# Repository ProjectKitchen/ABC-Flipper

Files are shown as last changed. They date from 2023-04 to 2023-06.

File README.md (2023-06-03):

# ABC-Flipper

**A Pinball Machine for solving Anagram Puzzles! (In cooperation with David Moises)**

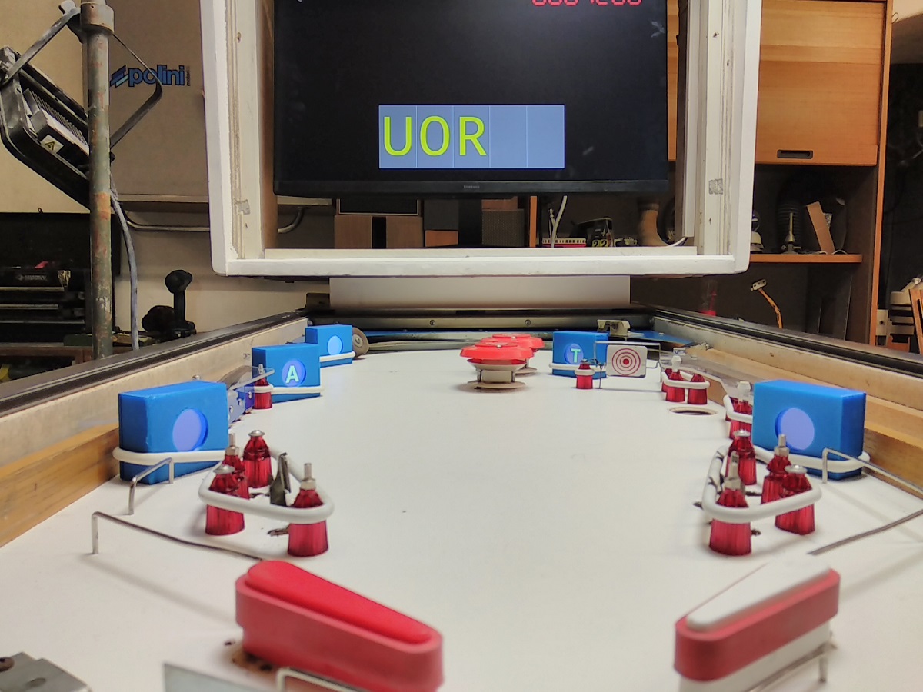
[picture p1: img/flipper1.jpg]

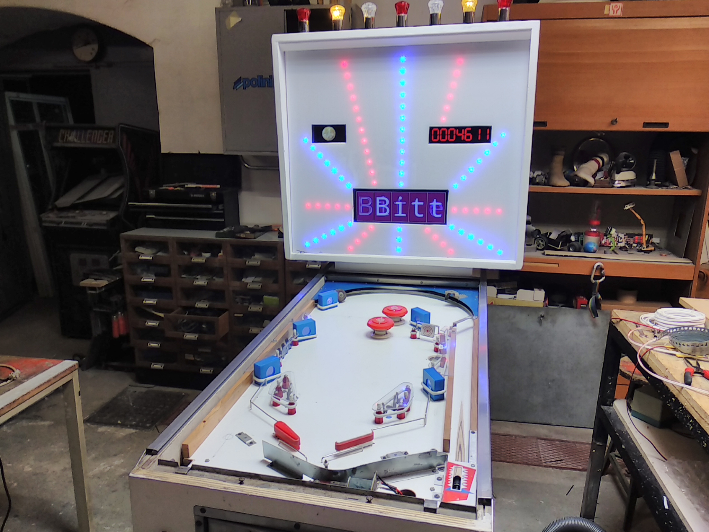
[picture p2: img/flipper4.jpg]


# Preparation

## Material

| Nr.  | Description | 
| ---- | --- |
| 1 | 1 x RaspberryPi 4 | 
| 2 | 1 x Teensy2.0++ (or Teensy3.2) |
| 3 | 5 x TeensyLC for Minidisplay Screens | 
| 4 | 2 x 8-Relay Module for Arduino | 
| 5 | 5 x SPI LCD Display (ST7735, 160x128, SPI) | 
| 6 | Breadboard, jumper wires, buttons/reed switches | 

## Install SW-Requirements

| Nr.  | Description | Source |
| ---- | --- | --- |
| 1 | Python3 | Open an command shell window and check your python/python3 version: `python3 --version'. The recommended version is python3.8 or newer |
| 2 | pyserial library | Install via pip: `pip3 install pyserial` |
| 3 | pygame library | Install via pip: `pip3 install pygame` |
| 4 | pillow library | Install via pip: `pip3 install pillow` |
| 5 | Arduino IDE | Download from Arduino website https://www.arduino.cc |
| 6 | Teensyduino Add-On | Download from website https://www.pjrc.com/teensy/td_download.html |
| 7 | Adafruit_GFX library | Install using Arduino library manager |
| 8 | Adafruit_ST7735 library | Install using Arduino library manager |

## Deploy Software

* Build and flash the Arduino code (folders src/arduinoIO and src/teensyLC_LCD) 
* Install custum fonts (copy segment.ttf to folder ~/.fonts, update font cache)
* run python3 flipper.py
* install startup script: sudo nano /etc/xdg/autostart/display.desktop, add:
    [Desktop Entry]
    Name=ABCFlipper
    Exec=/usr/bin/python3 /home/pi/ABC-Flipper/src/flipper.py

* configure read-only filesystem (Preferences -> RaspberryPi Configuration -> Performance)

## More photos

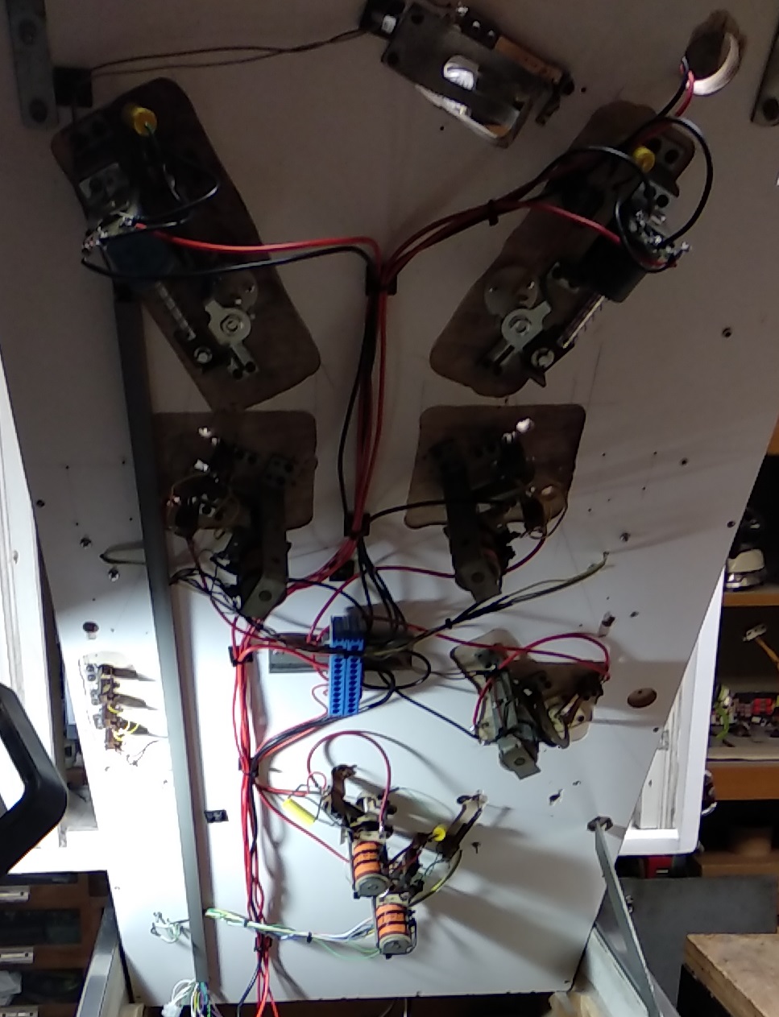
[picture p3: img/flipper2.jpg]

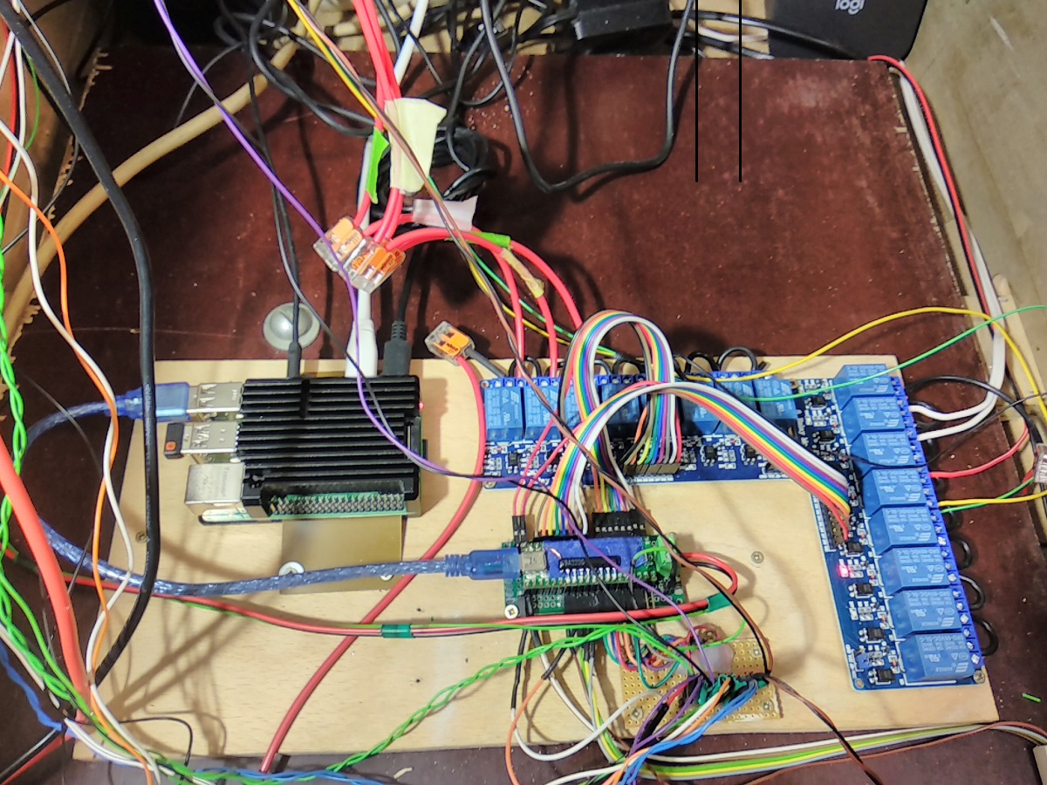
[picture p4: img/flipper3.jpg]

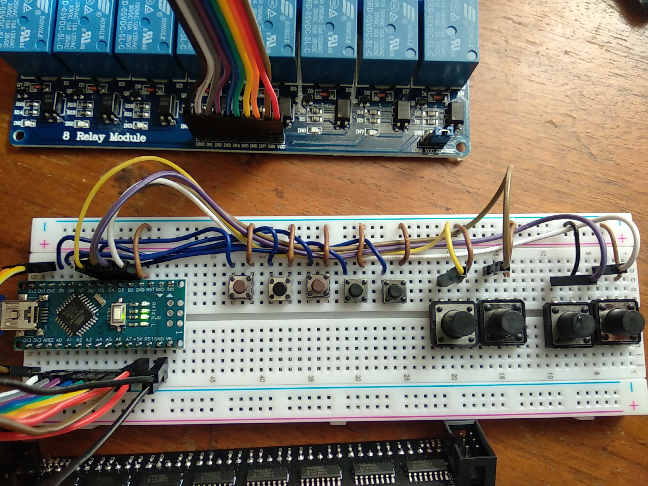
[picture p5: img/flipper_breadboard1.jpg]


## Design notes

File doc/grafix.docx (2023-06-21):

Anleitung:

Ziel des Spieles ist es, 5 Buchstaben zu treffen und daraus Worte zu bilden.
Das Spiel beginnt durch den Einwurf eines Zoomi-Coins. Pro Zoomi-Coin werden 3 Kugeln freigeschalten. Es gibt zwei unterschiedliche Spielvarianten: “Normal” und “Superhirn”. Den Superhin-Modus erkennt man daran, dass vor Spielbeginn abwechselnd der Zoomi-Coin und das Gehirn-Symbol am Flipper-Display abgebildet werden. Der Modus kann durch den Schalter im Inneren des Flippers gewechselt werden.

Spielmodus “Normal”: Getroffene Buchstaben erscheinen sofort an der richtigen Stelle des Wortes. Wird das Wort erraten, so erhält das erfolgreiche Team 1-5 Punkte (je mehr Buchstaben bereits gelöst waren, desto weniger Punkte!)

Spielmodus “Superhirn”: Buchstaben erscheinen in der Reihenfolge, in der sie getroffen wurden. Sobald alle 5 Buchstaben gesammelt wurden, ändert sich die Funktion der linken und rechten Flipper Taste: diese Tasten verschieben nun die Position eines Buchstaben! Eine Betätigung der FIX-Taste (an der Vorderseite) wechselt zum nächsten Buchstaben. Kann ein sinnvolles Anagramm gebildet werden, so erhält das erfolgreiche Team 5 Punkte, und die Kugel kommt zurück ins Spiel - verstreicht jedoch die verfügbare Zeit, ohne dass ein Wort gebildet werden konnte, geht die Kugel verloren!

Wird das Joker-Feld getroffen, werden alle 5 Buchstaben sogleich angezeigt. (Im Normalmodus wird dadurch das Wort gelöst, und das Team erhält 5 Punkte)

Wird ein Punkterekord (Highscore) am Flipper erzielt, kann der Name (bzw. die Initialen) eingegeben werden. Der aktuelle Buchstabe wird dabei durch Betätigen der linken oder rechten Flipper-Taste geändert, eine Betätigung der FIX-Taste wechselt zum nächsten Buchstaben.
Der Flipper kann auch in Teams gespielt werden: dabei versuchen alle Team-Mitglieder, das richtige Wort zu erraten!
Nach jedem Spiel kommt eine Person aus dem nächsten Team an die Reihe, die Punkte pro Team werden ggf. auf einem Zettel addiert.
(Diese manuelle Punktezählung ist unabhängig von der Punktezahl, die am Flipper erreicht wird.)

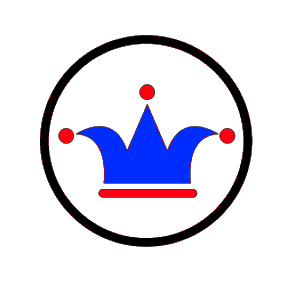
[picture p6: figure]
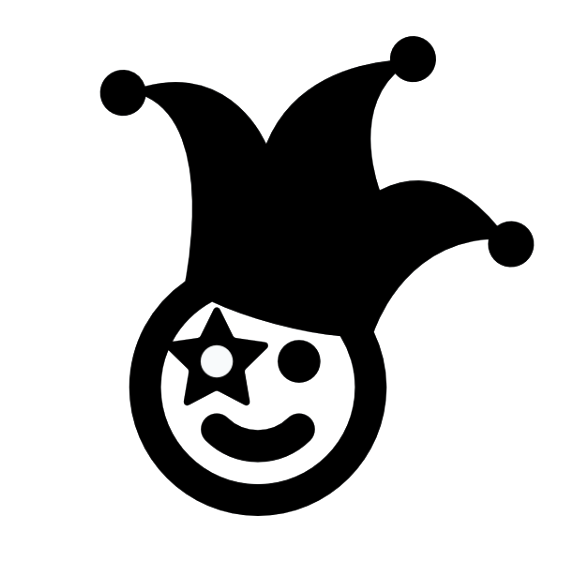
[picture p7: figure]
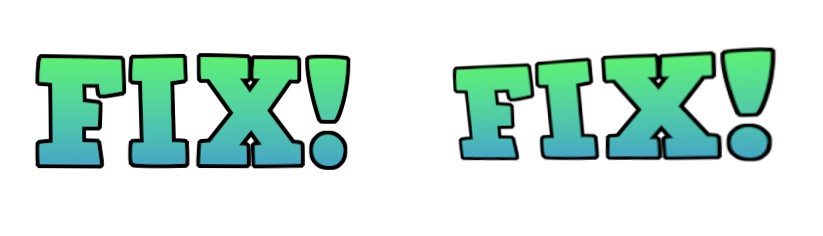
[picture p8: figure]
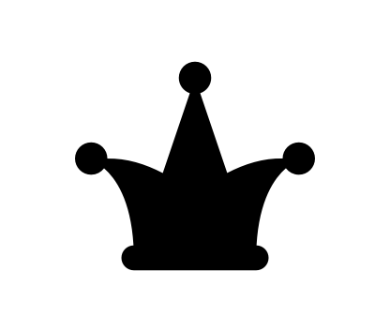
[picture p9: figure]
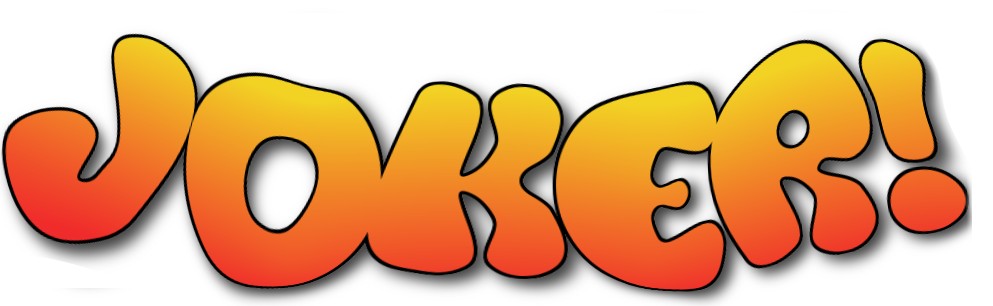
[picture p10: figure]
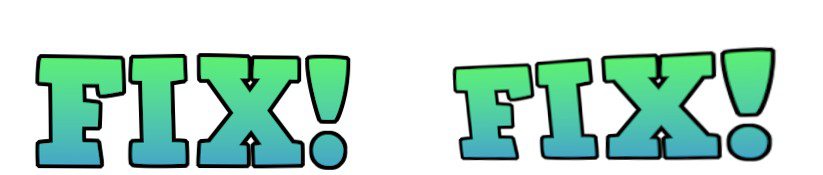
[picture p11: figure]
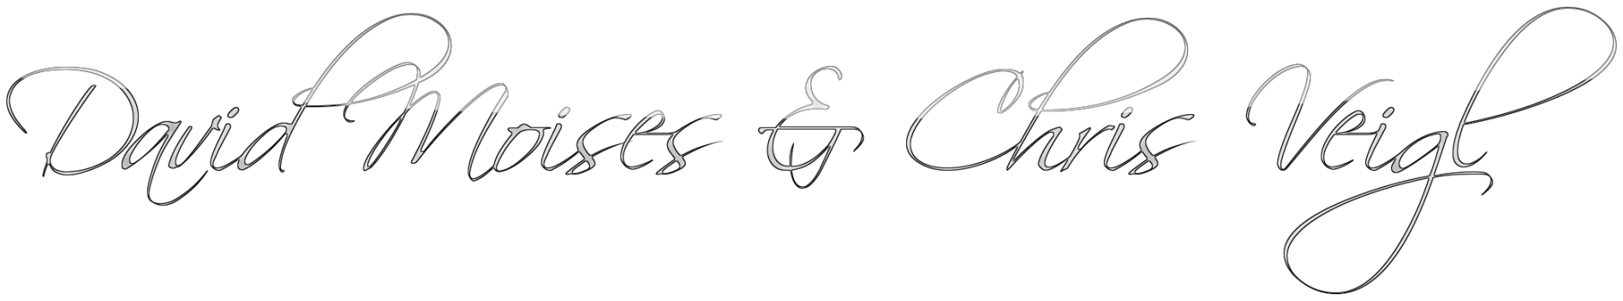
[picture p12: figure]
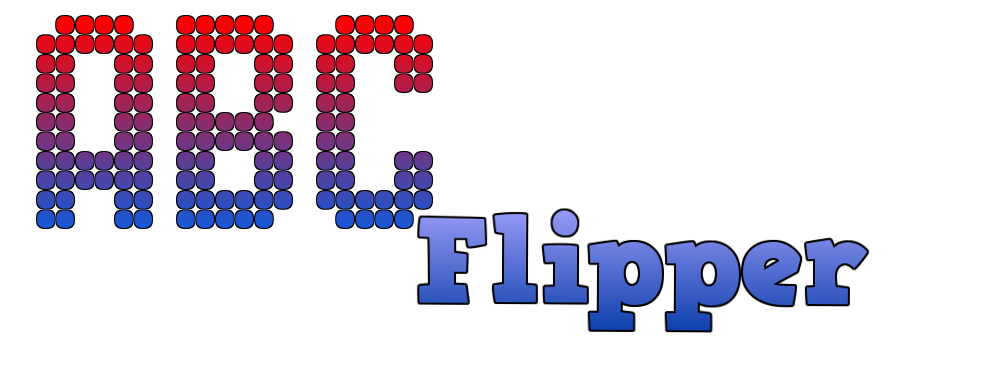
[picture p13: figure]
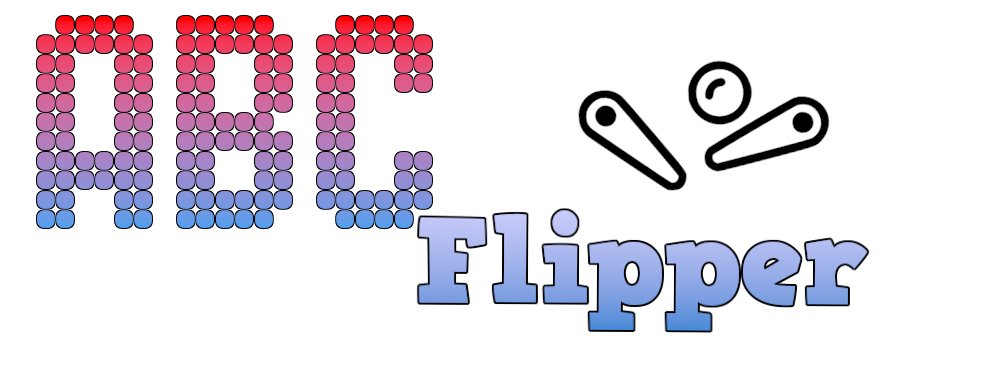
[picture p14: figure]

1. Wirf einen Zoomi ein (für 3 Kugeln)
2. Triff die Buchstaben!
3. Errate das Wort!
4. Bei Rekord: gib deinen Namen ein!

1. Wirf einen Zoomi ein!
2. Triff die Buchstaben!
3. Errate das Wort!
4. Bei Rekord: gib deinen Namen ein!

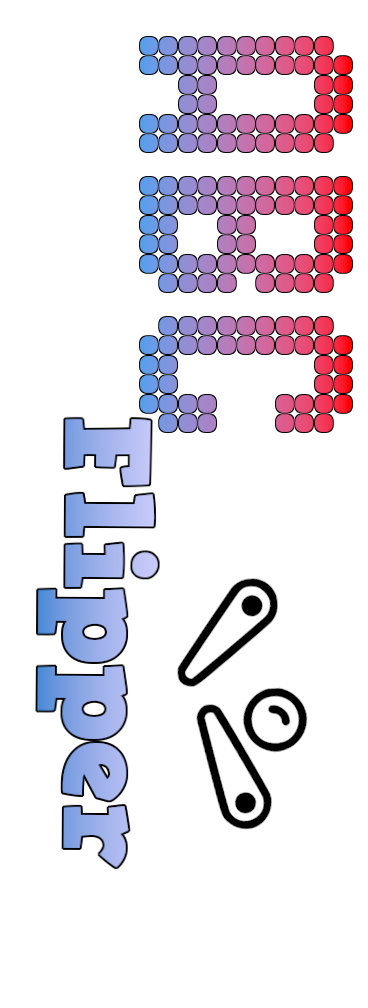
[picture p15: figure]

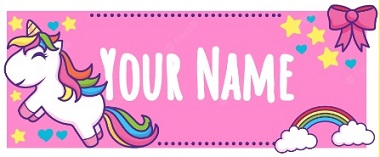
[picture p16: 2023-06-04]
img/name.jpg

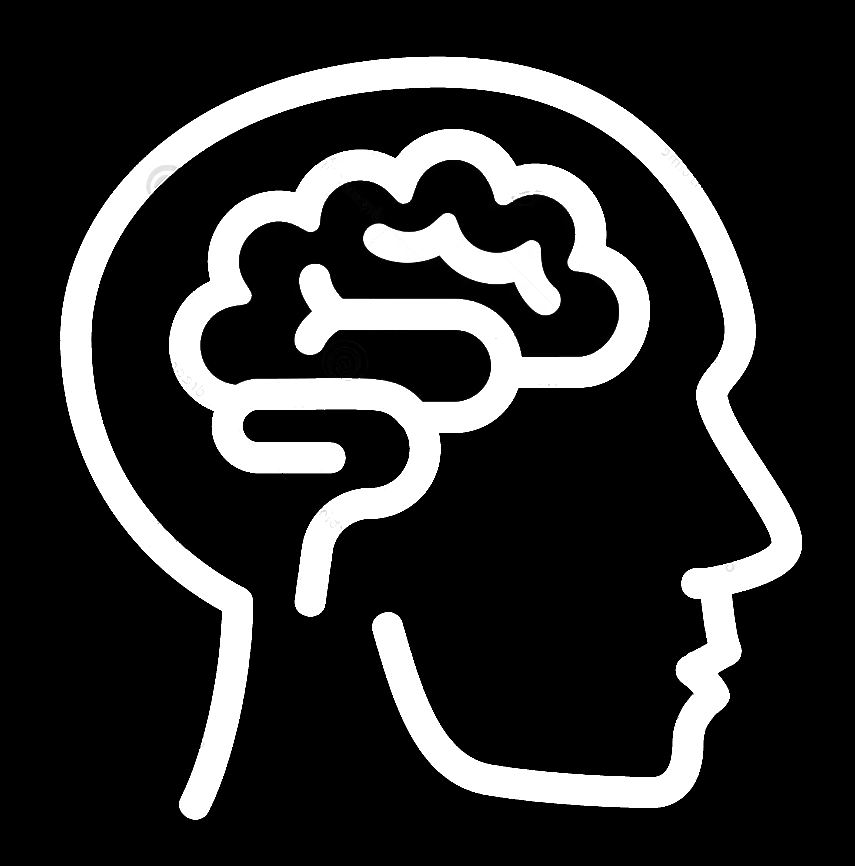
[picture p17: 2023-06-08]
img/brain.png

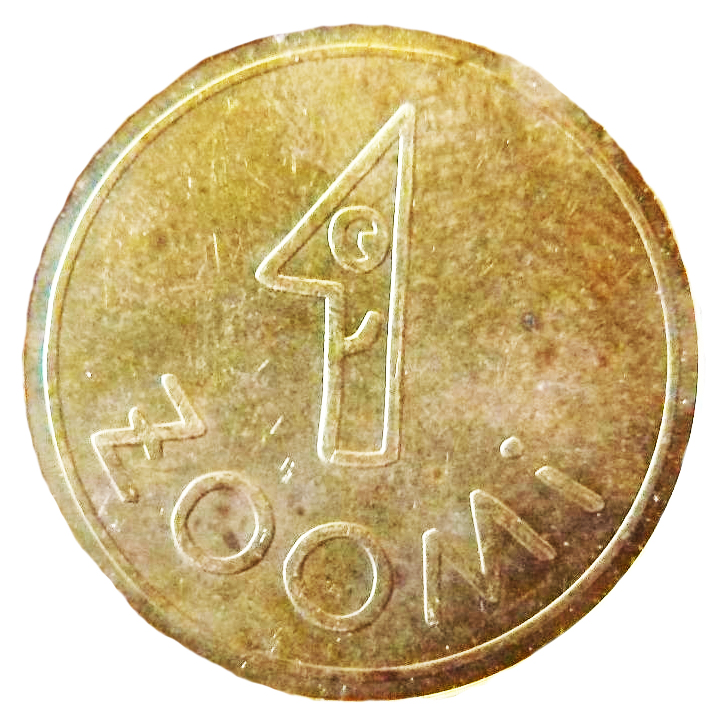
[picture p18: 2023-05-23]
img/ZOOMI_large.jpg

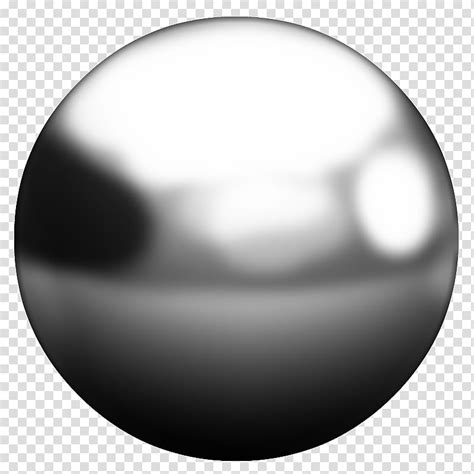
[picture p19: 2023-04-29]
img/pinball.png

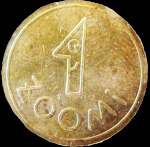
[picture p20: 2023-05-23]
img/coin.jpg

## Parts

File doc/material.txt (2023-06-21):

5x OLED SPI Display https://www.amazon.de/SSD1306-Display-Arduino-Raspberry-Schrift/dp/B07Z8QZLXS/
https://www.digikey.at/en/products/detail/adafruit-industries-llc/4741/13426655

https://luma-oled.readthedocs.io/en/latest/hardware.html#spi
https://www.brainy-bits.com/post/two-is-better-than-one-how-to-connect-two-spi-oled-displays
sudo python3 welcome.py -d st7735 -i spi --width 160 --height 128

1 x HDMI Screen:
https://www.samsung.com/hk_en/support/model/LS27C310EACXXK/

Port expander:
3x Adafruit MCP23017 I2C GPIO Expander
https://www.digikey.at/en/products/detail/adafruit-industries-llc/5346/15913270

Anagramme:
https://worter-finden.de/

Tkinter mainloop:
https://stackoverflow.com/questions/459083/how-do-you-run-your-own-code-alongside-tkinters-event-loop

8 7seg LED display SPI:
https://www.dfrobot.com/product-374.html
https://wiki.dfrobot.com/3-Wire_LED_Module__SKU_DFR0090_
https://www.dfrobot.com/product-568.html

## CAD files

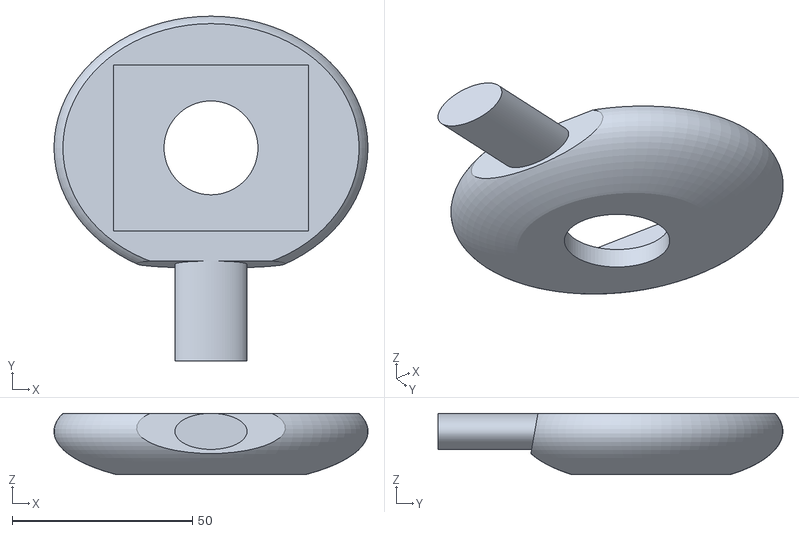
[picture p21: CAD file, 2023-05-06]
3Dprints/LCD-enclosure2.stl
87.0 x 95.5 x 17.0

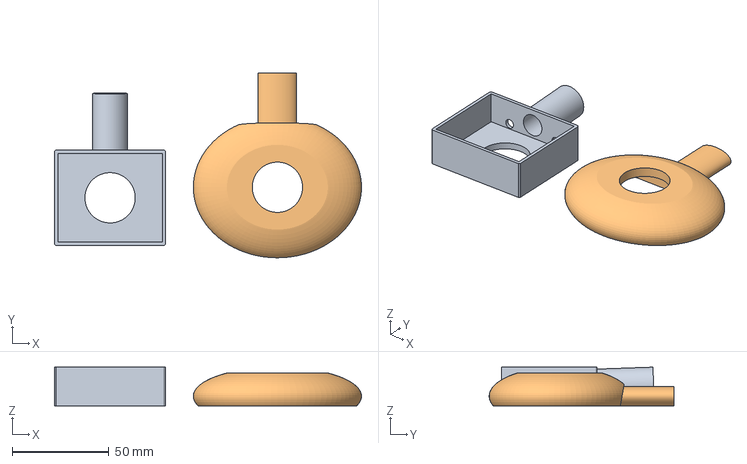
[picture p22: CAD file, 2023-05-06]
3Dprints/LCD-enclosure.3mf
158.8 x 95.5 x 20.0 mm
LCD-enclosure.stl
LCD-enclosure2.stl

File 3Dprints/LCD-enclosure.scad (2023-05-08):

$fs = 0.01;
$fn = 80;

l=54;
w=46;
h=22;
edge=2;
letterHole=13;
thickness=3.5;


module front() {
    difference() {
        linear_extrude(h)  square ([l+thickness,w+thickness],true);
        union() {
            translate ([-0, -0, -0.5])
              linear_extrude(l+1) {
                translate ([0, -0, -0]) circle(letterHole);
                translate ([l/2-edge+2,w/2-edge+2,0])
                    difference() {square(edge+2);circle(edge);}
                translate ([-(l/2-edge+2),(w/2-edge+2),0])
                    rotate(90) difference() {square(edge+1);circle(edge);}
                translate ([-(l/2-edge+2),-(w/2-edge+2),0])
                    rotate(180) difference() {square(edge+1);circle(edge);}
                translate ([(l/2-edge+2),-(w/2-edge+2),0])
                    rotate(270) difference() {square(edge+1);circle(edge);}
            }
        }
    }
}


module stand() {
 rotate([2,0,0]) 
 difference() {
    color("red")   rotate([90,0,0]) linear_extrude(20) scale([2,2,1]) circle(d=9);
 }
}

difference() {
  union() {
    // box
    difference() {
        front();
        translate ([0,0,-3])
           linear_extrude(h)  square ([l,w],true);
    }

    // stand
     translate ([0,-24,10]) stand();
   }
  union() {
   translate ([0,-20,9]) rotate([90,0,0]) cylinder(50,6,6);
   translate ([17,-20,9]) rotate([90,0,0]) cylinder(50,2.1,2.1);
   translate ([-17,-20,9]) rotate([90,0,0]) cylinder(50,2.1,2.1);
  }
}


color("blue")
 translate ([0,-80,0]) linear_extrude(2)  square ([l+thickness,w+thickness],true);

 translate ([0,-80 -w/2 +1.5,2]) linear_extrude(4)  square ([l-1,3],true);
 translate ([0,-80 +w/2 -1.5,2]) linear_extrude(4)  square ([l-1,3],true);


/*

color("green")
    translate([0, 30, 0])
        rotate_extrude($fn = 80)
            polygon( points=[[0,0],[8,4],[4,8],[4,12],[12,16],[0,20]] );
            
            
color("red")
    translate([10, -10, 0])
        linear_extrude(10)
            polygon( points=[[0,0],[8,4],[4,8],[4,12],[12,16],[0,20]] );
*/

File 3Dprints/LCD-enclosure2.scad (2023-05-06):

$fs = 0.01;
$fn = 80 ;


l=54;
w=46;
h=30;
add_l=33;
add_w=27;
letterHole=13;


difference() {

  difference() {
    color("red")
          translate ([-0, -0, 0])
            resize(newsize=[l+add_l,w+add_w,h]) sphere(r=1);

    union() {
      translate ([0,0,8])
         resize ([l, w, h])  cube(1, center=true);

      translate ([0,-83,0]) rotate ([-10,0,0])
         resize ([100, 100, 100])  cube(1, center=true);

      translate ([0,0,-37]) 
         resize ([100, 100, 50])  cube(1, center=true);
        
      }
    }


    union() {

   translate ([15,-20,-2.5]) rotate([90,0,0]) cylinder(10,2.5,2.5);
   translate ([-15,-20,-2.5]) rotate([90,0,0]) cylinder(10,2.5,2.5);        

   translate ([0,0,55])
            resize ([100, 100, 100])  cube(1, center=true);


        translate ([-0, -0, -50])
          linear_extrude(100) 
            circle(letterHole);
/*
        translate ([-4, -3, 0])
            cylinder(h=5,r=0.5, center=true);
        translate ([4, -3, 0])
            cylinder(h=5,r=0.5, center=true);
        translate ([-4, 3, 0])
            cylinder(h=5,r=0.5, center=true);
        translate ([4, 3, 0])
            cylinder(h=5,r=0.5, center=true);
*/
        translate ([0,0,-100])
            resize ([l, w, h])  cube(1, center=true);

    }
}


translate ([0,-29,0]) rotate([90,0,0])resize ([20,10,30]) cylinder(1,1,1);


/*

color("green")
    translate([0, 30, 0])
        rotate_extrude($fn = 80)
            polygon( points=[[0,0],[8,4],[4,8],[4,12],[12,16],[0,20]] );
            
            
color("red")
    translate([10, -10, 0])
        linear_extrude(10)
            polygon( points=[[0,0],[8,4],[4,8],[4,12],[12,16],[0,20]] );
*/

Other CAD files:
3Dprints/LCD-enclosure.stl

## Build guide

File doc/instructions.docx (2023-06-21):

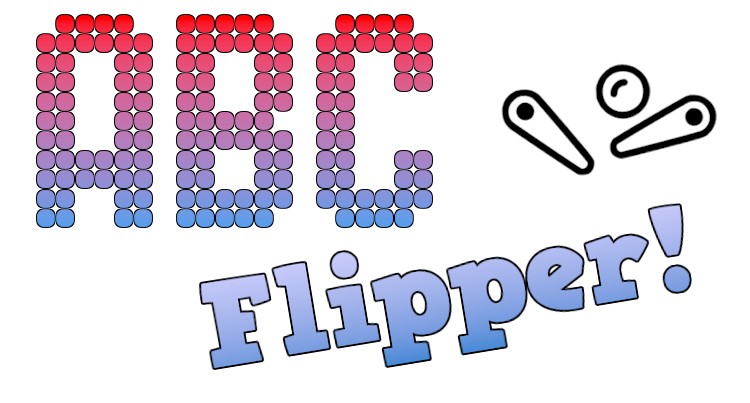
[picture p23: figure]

Anleitung:

Das Spiel beginnt durch den Einwurf eines Zoomi-Coins. Pro Zoomi-Coin werden 3 Kugeln freigeschalten.
Ziel des Spieles ist es, möglichst oft alle 5 Buchstaben zu treffen und daraus Worte zu bilden. Die zu treffenden Buchstaben erscheinen auf den 5 Mini-Displays des Flippers. Es gibt zwei unterschiedliche Spielvarianten: “Normal” und “Superhirn”. Den Superhin-Modus erkennt man daran, dass vor Spielbeginn ein Gehirn-Symbol abwechselnd mit dem Zoomi-Coin am Flipper-Display abgebildet wird.
(Der Modus kann durch einen Schalter im Inneren des Flippers gewechselt werden – bitte bei Bedarf beim Personal fragen.)

Spielmodus “Normal”: Getroffene Buchstaben erscheinen sofort an der richtigen Stelle des Wortes. Je mehr Buchstaben getroffen wurden, desto einfacher wird es, das Wort zu erraten. Das gelöste Wort bringt 1000 Punkte!

Spielmodus “Superhirn”: Buchstaben erscheinen in der Reihenfolge, in der sie getroffen wurden. Sobald alle 5 Buchstaben gesammelt wurden, ändert sich die Funktion der linken und rechten Flipper Taste: diese Tasten verschieben nun die Position eines Buchstaben! Eine Betätigung der FIX-Taste (an der Vorderseite) wechselt zum nächsten Buchstaben. Kann ein sinnvolles Anagramm gebildet werden, kommt die Kugel zurück ins Spiel und es gibt 1000 Punkte! Verstreicht jedoch die verfügbare Zeit, ohne dass ein Wort gebildet werden konnte, geht die Kugel verloren.

Wird das Joker-Feld getroffen, werden alle 5 Buchstaben angezeigt. 200 Extrapunkte! (Im Normal-Modus wird das Wort dadurch gelöst.)

Wird ein Punkterekord (Highscore) am Flipper erzielt, kann der Name oder die Initialen eingegeben werden. Dabei wird der aktuelle Buchstabe durch Betätigen der linken oder rechten Flipper-Taste geändert, das Drücken der FIX-Taste wechselt zum nächsten Buchstaben. (Der Highscore wird beim nächsten Neustart des Flippers wieder rückgesetzt.)

Der Flipper kann auch im Team gespielt werden: dabei versuchen alle, das richtige Wort zu erraten und helfen dadurch der Person, die am Gerät flippert! Optional können auch Punkte vergeben werden, wenn Personen oder Teams aus dem Publikum Worte erraten (zb. Punkte auf einem Zettel notieren).

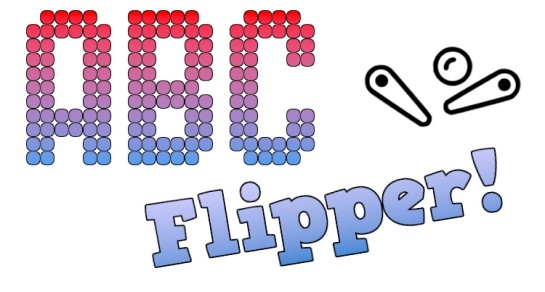
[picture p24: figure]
logo_komplett2

Versteckte Funktionen (“Eastereggs”): Solange kein Spiel läuft, können über die vordere “Fix”-Taste Morsezeichen eingegeben werden. Erkannte Buchstaben werden auf den Mini-Displays des Flippers dargestellt. Erfolgt über einen längeren Zeitraum keine Morse-Eingabe, werden die Displays gelöscht.
Auf diese Weise können Code-Worte eingegeben werden: ZOOMI erzeugt ein Freispiel ohne ein Einwurf eines Zoomi-Coins, BRAIN wechselt zwischen “Normal” und “Superhirn”-Modus,
ohne dass der Flipper geöffnet werden muss um den internen Schalter zu betätigen.

Wortliste und Software Updates: Die Wortliste und die Spielsoftware können bei Bedarf über einen WLAN-/Internetzugang erneuert werden. Die Source-Dateien sind über die Github-Adresse https://github.com/ProjectKitchen/ABC-Flipper verfügbar. Die Wortliste ist über folgenden Link einsehbar: https://raw.githubusercontent.com/ProjectKitchen/ABC-Flipper/main/src/worte.txt
Diese Liste kann bei Bedarf heruntergeladen, lokal verändert und per email gesendet werden (Kontaktadresse siehe unten), sodass der Wortumfang und der Schwierigkeitsgrad geändert werden können.

Betrieb und Wartung:

Der Flipper wird durch Einstecken der 230V-Spannungsversorgung gestartet und sollte nach etwa 2 Minuten betriebsbereit sein. Nach dem Betrieb kann einfach “der Stecker gezogen” werden. Sollte es während des Betriebs zu einem Software-Fehler kommen und der Flipper dadurch nicht mehr benutzbar sein, sollte ein Neustart versucht werden.

Der Flipper besitzt zwei Wartungsklappen, die durch unterschiedliche Schlüssel geöffnet werden können: Vordere Klappe (beim Münzeinwurf): Zugang zum Münzbehälter und zum Modus-Wechselschalter sowie zum Spiel-Start-Taster (gelb).
Hintere Klappe: Zugang zum Computermonitor (Source Select: HDMI etc.)

Probleme, Fragen & Feedback bitte per email an David Moises: hobbyextra@gmail.com und/oder Chris Veigl: chris.veigl@gmail.com

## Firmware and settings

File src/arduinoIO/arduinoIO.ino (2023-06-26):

//  arduinoIO.ino
//  interface to flipper.py
//  hardware: Teensy2.0++
//
//  buttons/sensors connected to in4-in17 
//  relais connected to out18-out25 (lights) and out38-out45(magnets)

#define NUM_BUTTONS 13
#define FIRST_BUTTON 4

#define NUM_RELAIS   8
#define FIRST_RELAIS 38

#define BALL_RELAIS 38
#define THROWER2_RELAIS 39
#define THROWER1_RELAIS 40
#define BELL_RELAIS 41

#define NUM_LIGHTS 8
#define FIRST_LIGHT 18

#define NUM_TOPLIGHTS 3
#define FIRST_TOPLIGHT 18

#define NUM_RANDOMLIGHTS 4
#define FIRST_RANDOMLIGHT 22

#define BUMPERLIGHT_RELAIS 21

#define THROWER1_BUTTON 6
#define THROWER2_BUTTON 8
#define JOKER_BUTTON   14
#define BUMPER_BUTTON  13
#define MODE_SWITCH    17


#define BELL_DURATION 100
#define BALL_DURATION 100
#define BUMPERLIGHT_DURATION 200
#define BUTTON_DEBOUNCE_CYCLES  4
#define BUTTON_BYPASS_TIME 100
#define FLIPPERCOIL_MAXTIME 15000
#define FLIPPER_BYPASS_TIME 5000

int blinkIdleTime = 2000;
int blinkGameTime = 750;
int blinkActiveTime = 500;
int blinkWinTime = 200;
int bellOnTime = 0, ballOnTime = 0, bumperLightOnTime = 0, topLightBlink = 0;
int thr1Count = 0, thr2Count = 0, flipper1Bypass = 0, flipper2Bypass = 0;
int autoSolve=-1;

uint8_t buttonState[NUM_BUTTONS] = {0};
uint8_t buttonDebounce[NUM_BUTTONS] = {0};
uint32_t buttonTimestamp[NUM_BUTTONS] = {0};

#define GAMESTATE_IDLE    'a'
#define GAMESTATE_FLIPPER 'b'
#define GAMESTATE_ANAGRAM 'c'
#define GAMESTATE_WON     'd'
#define GAMESTATE_LOST    'e'

#define CMD_TRIGGER_BALL  'f'
#define CMD_TRIGGER_BELL  'g'
#define CMD_BUMPER_LIGHT  'i'
#define CMD_RANDOM_LIGHT  'h'
#define CMD_TOP_LIGHT     'j'


int gameState = GAMESTATE_IDLE;
int blinkCount = 0;
int blinkPos = 0;


void setup() {

  Serial.begin(115200);
  Serial1.begin (9600);

  pinMode(MODE_SWITCH,INPUT_PULLUP);
  for (int i = FIRST_BUTTON; i < FIRST_BUTTON + NUM_BUTTONS; i++) {
    pinMode(i, INPUT_PULLUP);
  }

  for (int i = FIRST_RELAIS; i < FIRST_RELAIS + NUM_RELAIS; i++) {
    pinMode(i, OUTPUT); digitalWrite(i, HIGH);
  }
  digitalWrite (BALL_RELAIS, LOW);
  digitalWrite (THROWER1_RELAIS, LOW);
  digitalWrite (THROWER2_RELAIS, LOW);

  for (int i = FIRST_LIGHT; i < FIRST_LIGHT + NUM_LIGHTS; i++) {
    pinMode(i, OUTPUT); digitalWrite(i, HIGH);
  }

  Serial.print('s');
}


void setRandomLights(uint8_t mode) {
  //uint8_t pattern=random(1<<NUM_RANDOMLIGHTS);
  static uint8_t pattern = 4;
  if (mode == 1) {
    if (pattern == 4) pattern = 8; else pattern = 4;
  }
  else if (mode == 2) {
    if (pattern == 12) pattern = 0; else pattern = 12;
  }
  if (!mode) pattern = 0; // clear all lights

  for (uint8_t i = 0; i < NUM_RANDOMLIGHTS; i++)
    if (pattern & (1 << i)) digitalWrite(FIRST_RANDOMLIGHT + i, LOW);
    else digitalWrite(FIRST_RANDOMLIGHT + i, HIGH);
}

void setTopLights(uint8_t mode) {

  for (uint8_t i = 0; i < NUM_TOPLIGHTS; i++)
    if (mode) digitalWrite(FIRST_TOPLIGHT + i, LOW);
    else digitalWrite(FIRST_TOPLIGHT + i, HIGH);

}

void processBlinks() {
  switch (gameState) {

    case GAMESTATE_IDLE:
      if (++blinkCount > blinkIdleTime) {
        blinkCount = 0;
        digitalWrite(FIRST_TOPLIGHT + blinkPos, HIGH);
        if (++blinkPos >= NUM_TOPLIGHTS) blinkPos = 0;
        digitalWrite(FIRST_TOPLIGHT + blinkPos, LOW);
        if (random(20) > 5) setRandomLights(1);

        if (digitalRead(MODE_SWITCH) != autoSolve) {
          autoSolve=digitalRead(MODE_SWITCH);
          if (autoSolve == LOW) Serial.print ('='); else  Serial.print ('>');          
        }

      }
      break;
    case GAMESTATE_FLIPPER:
      if (++blinkCount > blinkGameTime) {
        blinkCount = 0;
        switch (random(3)) {
          case 0:
            digitalWrite(FIRST_TOPLIGHT, HIGH);
            digitalWrite(FIRST_TOPLIGHT + 1, LOW);
            digitalWrite(FIRST_TOPLIGHT + 2, LOW);
            break;
          case 1:
            digitalWrite(FIRST_TOPLIGHT, LOW);
            digitalWrite(FIRST_TOPLIGHT + 1, HIGH);
            digitalWrite(FIRST_TOPLIGHT + 2, LOW);
            break;
          case 2:
            digitalWrite(FIRST_TOPLIGHT, LOW);
            digitalWrite(FIRST_TOPLIGHT + 1, LOW);
            digitalWrite(FIRST_TOPLIGHT + 2, HIGH);
            break;

        }
      }
      break;

    case GAMESTATE_ANAGRAM:
      if (++blinkCount > blinkActiveTime) {
        setRandomLights(2);
        blinkCount = 0;
        digitalWrite(FIRST_TOPLIGHT + blinkPos, HIGH);
        if (++blinkPos >= NUM_TOPLIGHTS) blinkPos = 0;
        digitalWrite(FIRST_TOPLIGHT + blinkPos, LOW);
      }
      break;

    case GAMESTATE_WON:
      if (++blinkCount > blinkWinTime) {
        blinkCount = 0;
        setRandomLights(2);
        for (int i = 0; i < NUM_TOPLIGHTS; i++)
          digitalWrite(FIRST_TOPLIGHT + i, HIGH);
        if (++blinkPos >= 5) {
          blinkPos = 0;
          blinkCount = 0;
          gameState = 'a';
        }

      }
      if (blinkCount == blinkWinTime / 2) {
        for (int i = 0; i < NUM_TOPLIGHTS; i++)
          digitalWrite(FIRST_TOPLIGHT + i, LOW);
      }
      break;
    case GAMESTATE_LOST:
      break;
  }
}


void loop() {

  int tmp;
  for (int i = 0; i < NUM_BUTTONS; i++) {

    tmp = digitalRead(FIRST_BUTTON + i);
    if ((tmp == LOW) && (buttonDebounce[i] < BUTTON_DEBOUNCE_CYCLES)) {
      buttonDebounce[i]++;
      if ((buttonDebounce[i] == BUTTON_DEBOUNCE_CYCLES) && !buttonState[i])  {
        buttonState[i] = 1;
        // handle button press
        if ((millis() - buttonTimestamp[i]) > BUTTON_BYPASS_TIME) {
          buttonTimestamp[i] = millis();
          Serial.print((char) ('0' + i));
          if (FIRST_BUTTON + i == BUMPER_BUTTON) {
            bumperLightOnTime = BUMPERLIGHT_DURATION;
            digitalWrite(BUMPERLIGHT_RELAIS, LOW);
          }
        }
      }
    }

    if ((tmp == HIGH) && (buttonDebounce[i] > 0)) {
      buttonDebounce[i]--;
      if ((buttonDebounce[i] == 0) && buttonState[i])  {
        buttonState[i] = 0;
        // if desired, handle button release
        if ((gameState==GAMESTATE_IDLE) && (i==3)) {
          Serial.print('.');  // send release info for fix/morse key
        }
      }
    }
  }


  if (Serial.available()) {
    int c = Serial.read();
    if ((c >= GAMESTATE_IDLE) && (c <= GAMESTATE_LOST)) {
      gameState = c;
      blinkPos = 0; blinkCount = 0;
      setRandomLights(0);
      setTopLights(0);
      if (c==GAMESTATE_IDLE) {
          autoSolve=digitalRead(MODE_SWITCH);
          if (autoSolve == LOW) Serial.print ('='); else  Serial.print ('>'); 
      }

    }
    else if (c == CMD_TRIGGER_BELL) {
      digitalWrite(BELL_RELAIS, LOW);
      bellOnTime = BELL_DURATION;
    }
    else if (c == CMD_TRIGGER_BALL) {
      digitalWrite(BALL_RELAIS, HIGH);
      ballOnTime = BALL_DURATION;
    }
    else if (c == CMD_BUMPER_LIGHT) {
      bumperLightOnTime = BUMPERLIGHT_DURATION;
      digitalWrite(BUMPERLIGHT_RELAIS, LOW);
    }
    else if (c == CMD_RANDOM_LIGHT) {
      setRandomLights(1);
    }
    else if (c == CMD_TOP_LIGHT) {
      topLightBlink = 800;
    }
    else Serial1.write((byte)c);
  }

  if (bellOnTime) {
    bellOnTime--;
    if (!bellOnTime) digitalWrite(BELL_RELAIS, HIGH);
  }

  if (ballOnTime) {
    ballOnTime--;
    if (!ballOnTime) digitalWrite(BALL_RELAIS, LOW);
  }

  if (bumperLightOnTime) {
    bumperLightOnTime--;
    if (!bumperLightOnTime) digitalWrite(BUMPERLIGHT_RELAIS, HIGH);
  }

  if (topLightBlink) {
    topLightBlink--;
    if ((topLightBlink % 300) < 200) setTopLights(1);
    else setTopLights(0);
    if (!topLightBlink) setTopLights(0);
  }


  // control flipper coils via buttons
  if ((gameState == GAMESTATE_FLIPPER) || (gameState == GAMESTATE_WON)) {

    if (!digitalRead(THROWER1_BUTTON)) {
      if ((thr1Count < FLIPPERCOIL_MAXTIME) && (!flipper1Bypass)) {
        thr1Count++;
        if (thr1Count == FLIPPERCOIL_MAXTIME) flipper1Bypass = FLIPPER_BYPASS_TIME;
        else digitalWrite(THROWER1_RELAIS, HIGH);
      }

    }
    else {
      thr1Count = 0;
      digitalWrite(THROWER1_RELAIS, LOW);
    }
    if (flipper1Bypass) {
      flipper1Bypass--;
      digitalWrite(THROWER1_RELAIS, LOW);
    }

    if (!digitalRead(THROWER2_BUTTON)) {
      if ((thr2Count < FLIPPERCOIL_MAXTIME) && (!flipper2Bypass)) {
        thr2Count++;
        if (thr2Count == FLIPPERCOIL_MAXTIME) flipper2Bypass = FLIPPER_BYPASS_TIME;
        else digitalWrite(THROWER2_RELAIS, HIGH);
      }

    }
    else {
      thr2Count = 0;
      digitalWrite(THROWER2_RELAIS, LOW);
    }
    if (flipper2Bypass) {
      flipper2Bypass--;
      digitalWrite(THROWER2_RELAIS, LOW);
    }

  } else {
    // deactivate throwers!
    digitalWrite (THROWER1_RELAIS, LOW);
    digitalWrite (THROWER2_RELAIS, LOW);
  }

  processBlinks();
  delay(1);   //  1kHz main loop
}

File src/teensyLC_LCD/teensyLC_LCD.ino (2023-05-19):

// for font customisation use:
//  https://tchapi.github.io/Adafruit-GFX-Font-Customiser/
//  https://github.com/adafruit/Adafruit-GFX-Library/tree/master/Fonts


#include <Adafruit_GFX.h>     // Core graphics library
#include <Adafruit_ST7735.h>  // Hardware-specific library for ST7735
#include <SPI.h>
#include "FreeSansBold24pt7b.h"

#define ECHO_SERIAL_INPUT 0  // 1 for serial debug output

#define XPOS 35
#define YPOS 100


#define CMD_ROTATE '7'
#define CMD_GOIDLE '8'

// These pins will also work for the 1.8" TFT shield.
#define TFT_CS 10
#define TFT_RST -1  // Or set to -1 and connect to Arduino RESET pin
#define TFT_DC 8


#define MODE_IDLE   0
#define MODE_LETTER 1
#define MODE_HIT    2

// For 1.44" and 1.8" TFT with ST7735 use:
Adafruit_ST7735 tft = Adafruit_ST7735(TFT_CS, TFT_DC, TFT_RST);

char text[] = "?";
uint8_t displayNum = 0;
int mode = MODE_IDLE;
uint32_t animTimestamp = 0;
int animState = 0;
int actRotation = 3;

void setup(void) {
  Serial.begin(9600);
  Serial1.begin(9600);

  // Use this initializer if using a 1.8" TFT screen:
  tft.initR(INITR_BLACKTAB);  // Init ST7735S chip, black tab
  // tft.initR(INITR_GREENTAB);      // Init ST7735S chip, green tab
  tft.setSPISpeed(40000000);
  tft.fillScreen(ST77XX_BLACK);

  delay(500);
  randomSeed(analogRead(0));
  tft.setRotation(actRotation);
  tft.setFont(&FreeSansBold24pt7b);
  tft.setTextSize(2);
  //tft.setTextSize(13);

  tft.fillScreen(ST77XX_BLACK);
  animTimestamp = 0;

  /*
    for (int i=65;i<255;i++) {
      text[0]=i;
      tft.fillScreen(ST77XX_BLACK);
      tft.setCursor(60, 100);  // 63, 100
      tft.setTextColor(ST77XX_YELLOW);
      tft.println(text);
      delay(300);
    }
  */

}

void processMode() {
  switch (mode) {
    case MODE_IDLE:
      if (millis() > animTimestamp) {
        animTimestamp = millis() + random(300, 5000);
        animState++;
        if (animState == 1) {
          tft.setCursor(XPOS, YPOS);
          tft.setTextColor(ST77XX_MAGENTA);
          tft.println("?");
        } else {
          tft.fillScreen(ST77XX_BLACK);
          animState = 0;
        }
      }
      break;
    case MODE_LETTER:
      break;
    case MODE_HIT:
      if (millis() > animTimestamp) {
        if (ECHO_SERIAL_INPUT) Serial.print("*");
        animTimestamp = millis() + 50;
        animState++;
        if (animState < 15) {
          if (animState % 2) tft.invertDisplay(true);
          else tft.invertDisplay(false);
        }
        else {
          tft.invertDisplay(false);
          tft.fillScreen(ST77XX_BLACK);
          //tft.setCursor(XPOS, YPOS);
          //tft.setTextColor(ST77XX_GREEN);
          //tft.println("o");
          mode = MODE_LETTER;
        }
      }
      break;
  }
  return;
}


void loop() {
  int input = -1;
  if (Serial.available()) input = Serial.read();
  else if (Serial1.available()) input = Serial1.read();
  if (input == -1) {
    processMode();
    return;
  }

  if (ECHO_SERIAL_INPUT) Serial.println((int) input);

  if (input == CMD_ROTATE) {
    actRotation = (actRotation + 1) % 4;
    tft.setRotation(actRotation);
    tft.fillScreen(ST77XX_BLACK);
    Serial1.write(CMD_ROTATE);
    return;
  }

  if (input == CMD_GOIDLE) {
    mode = MODE_IDLE;
    tft.fillScreen(ST77XX_BLACK);
    Serial1.write(CMD_GOIDLE);
    return;
  }

  if ((input > '0') && (input < '6')) {
    displayNum = input;
  } else {
    if (displayNum == '1') {
      if (text[0] != input) {
        text[0] = input;
        if (input != ' ') {
          tft.fillScreen(ST77XX_BLACK);
          tft.setCursor(XPOS, YPOS);
          tft.setTextColor(ST77XX_YELLOW);
          tft.println(text);
          displayNum = 0;
          mode = MODE_LETTER;
          if (ECHO_SERIAL_INPUT) Serial.println("mode: Letter");
        }
      }
      if (input == ' ') {
        mode = MODE_HIT;
        animState = 0;
        if (ECHO_SERIAL_INPUT) Serial.println("mode: Hit");
      }
    } else {
      Serial1.write(displayNum - 1);
      Serial1.write((uint8_t)input);
      displayNum = 0;
    }
  }
}


// tft.invertDisplay(true);
// delay(500);
// tft.invertDisplay(false);
//  tft.setCursor(0, 20);    // 63, 20
//  tft.setTextColor(ST77XX_BLACK);
//  tft.println(text);

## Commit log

2023-04-23 added first low level IO using Arduino
2023-05-02 added 3d prints
    [LCD-enclosure.scad, LCD-enclosure2.scad]
2023-05-02 added/updated lcd enclosures
    [LCD-enclosure.3mf, LCD-enclosure.scad, LCD-enclosure.stl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]
2023-05-04 modified 3d enclosure
    [LCD-enclosure.3mf, LCD-enclosure.scad, LCD-enclosure.stl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]
2023-05-06 route serial comminication for display, changed pinout for teensy
2023-05-06 renamed files for teensyLC
2023-05-08 modified enclosure
    [LCD-enclosure.scad, LCD-enclosure.stl]
2023-05-13 teensy 2.0++ compatibility
2023-05-14 fixed lostAnim race condition
    [flipper.py]
2023-05-23 updated pin connections
2023-06-04 solved clock position bug
    [flipper.py]
2023-06-04 added flipper coil maxtime
    [arduinoIO.ino]
2023-06-11 flippers active also in won mode
    [arduinoIO.ino]
2023-06-26 invert logic for SSR relais
    [arduinoIO.ino]
2023-06-26 prevent clear of LCDs when no morse text was entered
    [flipper.py]
2023-07-16 fixed 6 letters bug
    [flipper.py]
